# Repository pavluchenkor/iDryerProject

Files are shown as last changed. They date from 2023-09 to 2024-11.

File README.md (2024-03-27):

# Проект

Варианты сборки сушилки могут значительно отличаться. Сушилка iDryer может собираться как на одну так и на 10 катушек, в различных корпусах и разнообразными нагревательными элементами и вариантами обеспечения необходимой конвекции.

Ознакомьтесь с существующими решениями  

<div class="grid cards" markdown>
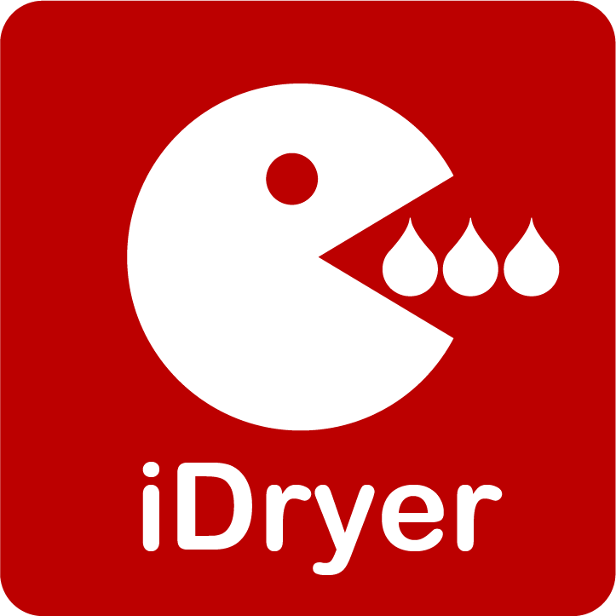
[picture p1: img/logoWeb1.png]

[Прошивка](/iDryerV2/Firmware/iDryerController/)  [:material-arrow-right-box:](/iDryerV2/Firmware/iDryerController/) 
</div>

<div class="grid cards" markdown>
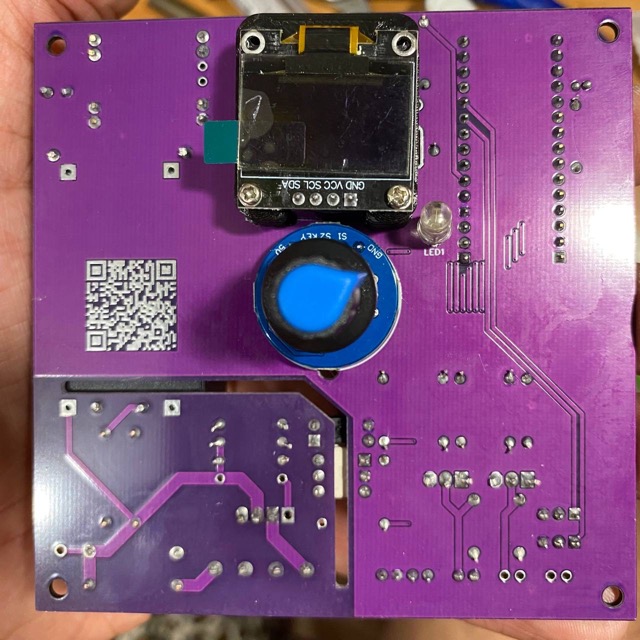
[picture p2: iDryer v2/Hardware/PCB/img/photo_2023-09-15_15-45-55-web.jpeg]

[Файлы печатной платы](/iDryerV2/Hardware/iDryerProject/iDryer%20v2/Hardware/PCB/)  [:material-arrow-right-box:](/iDryerV2/Hardware/iDryerProject/iDryer%20v2/Hardware/PCB/)           
</div>

<div class="grid cards" markdown>
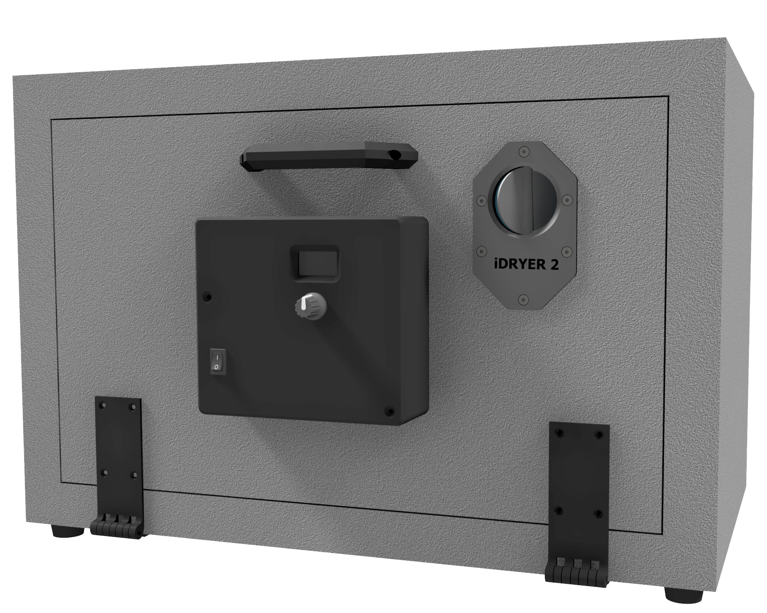
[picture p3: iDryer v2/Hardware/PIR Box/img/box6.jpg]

[Раскрой и инструкция по сборке корпуса из PIR плиты](/iDryerV2/Hardware/iDryerProject/iDryer%20v2/Hardware/PIR%20Box/)  [:material-arrow-right-box:](/iDryerV2/Hardware/iDryerProject/iDryer%20v2/Hardware/PIR%20Box/)                  
</div>

<div class="grid cards" markdown>
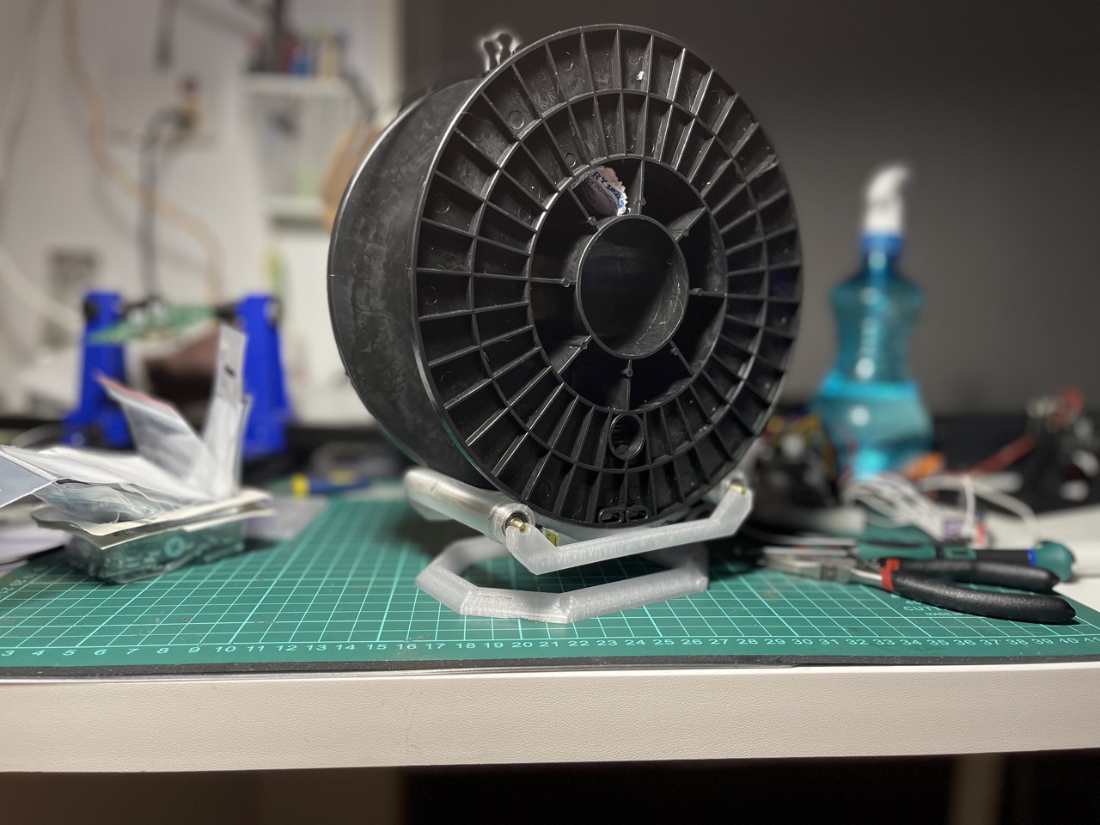
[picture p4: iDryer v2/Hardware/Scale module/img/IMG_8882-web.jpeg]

[Держатель катушек совмещенный с модулем весов](/iDryerV2/Hardware/iDryerProject/iDryer%20v2/Hardware/Scale%20module/)        [:material-arrow-right-box:](/iDryerV2/Hardware/iDryerProject/iDryer%20v2/Hardware/Scale%20module/)                           
</div>

<div class="grid cards" markdown>
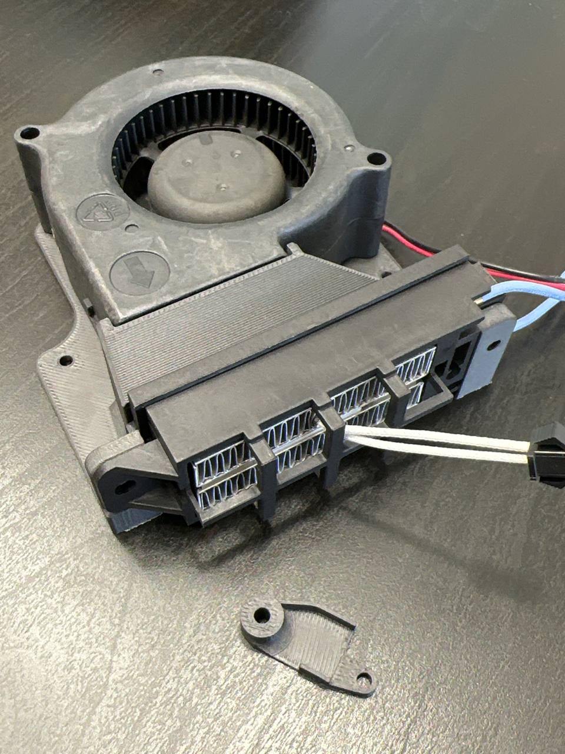
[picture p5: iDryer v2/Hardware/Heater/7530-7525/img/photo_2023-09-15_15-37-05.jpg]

[Сборка кулера 7530 и нагревательного элемента](/iDryerV2/Hardware/iDryerProject/iDryer%20v2/Hardware/Heater/7530-7525/)   [:material-arrow-right-box:](/iDryerV2/Hardware/iDryerProject/iDryer%20v2/Hardware/Heater/7530-7525/)                           
</div>

<div class="grid cards" markdown>
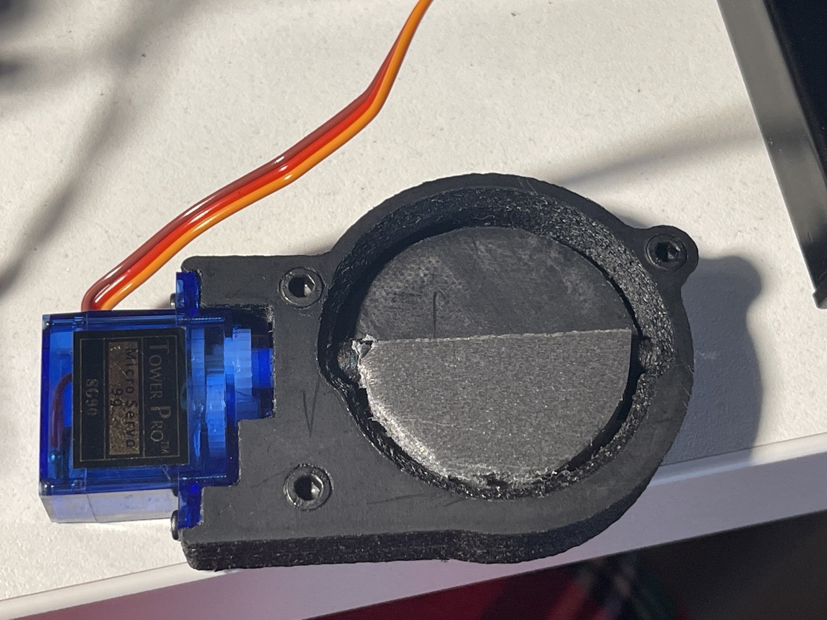
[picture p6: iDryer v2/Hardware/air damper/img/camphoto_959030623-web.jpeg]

[Воздушная заслонка v1](/iDryerV2/Hardware/iDryerProject/iDryer%20v2/Hardware/air%20damper/)  [:material-arrow-right-box:](/iDryerV2/Hardware/iDryerProject/iDryer%20v2/Hardware/air%20damper/)                                                             
</div>

<div class="grid cards" markdown>
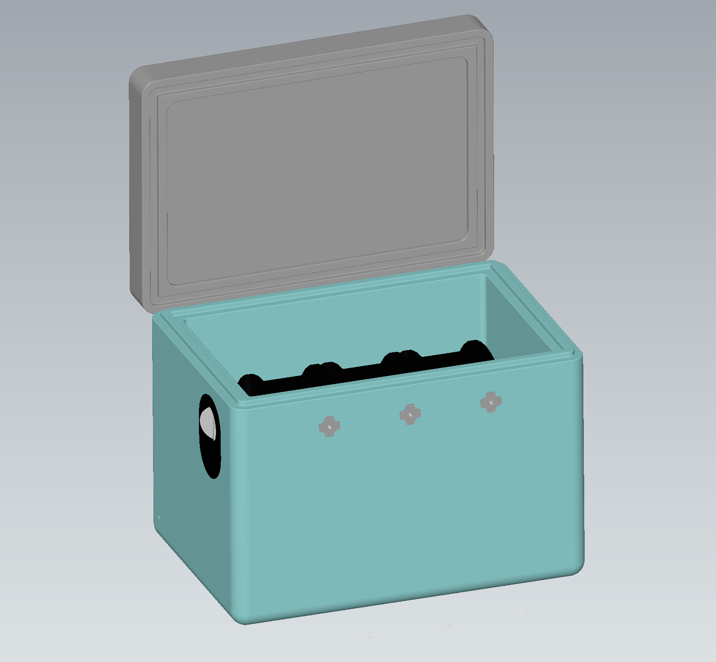
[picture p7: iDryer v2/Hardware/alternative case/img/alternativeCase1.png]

[Коробка из EPP, относительно ударопрочный и теплоизоляционный материал](/iDryerV2/Hardware/iDryerProject/iDryer%20v2/Hardware/alternative%20case/)      [:material-arrow-right-box:](/iDryerV2/Hardware/iDryerProject/iDryer%20v2/Hardware/alternative%20case/)                                                      
</div>

<div class="grid cards" markdown>
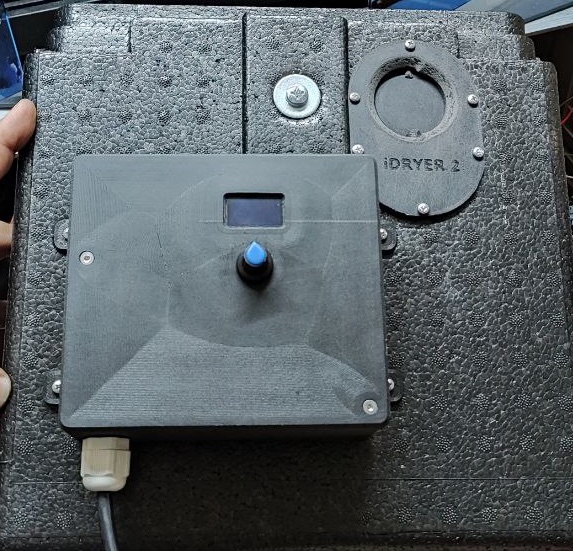
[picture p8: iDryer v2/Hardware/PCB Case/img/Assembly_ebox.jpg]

[Корпус контроллера, печатные детали](/iDryerV2/Hardware/iDryerProject/iDryer%20v2/Hardware/PCB%20Case/) [:material-arrow-right-box:](/iDryerV2/Hardware/iDryerProject/iDryer%20v2/Hardware/PCB%20Case/)                                                 
</div>

[группа в телеграмм :fontawesome-solid-paper-plane:](https://t.me/iDryer){ .md-button }

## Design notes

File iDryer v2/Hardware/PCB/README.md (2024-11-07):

**iDryer v2.1**

***Текущая версия***

Вы можете самостоятельно заказать изготовление печатной платы и приобрести необходимые компоненты. 
Если Вы имеете минимальный опыт пайки, то сборка не составит труда, все компоненты выводные и имеют крупный размер, а участники группы всегда помогут советом.

!!! warning annotate "Файлы для скачивания r2.1"

    PCB Design r2.1 [jlcpcb.com](https://oshwlab.com/svet_team/idryer_copy_copy)

    BOM для самостоятельной сборки r2.1 [google docs](https://docs.google.com/spreadsheets/d/1Y0MG9n_SadcK8cb_-e9J9ABQYqM_iH7iXZHlKbaz7wk/edit?usp=sharing)

## r2.1
<!-- ![печатная плата r2.1](https://raw.githubusercontent.com/pavluchenkor/iDryerProject/main/iDryer%20v2/Hardware/PCB/img/img2023-12-12-1.png){.image-container}<br>
![печатная плата r2.1](https://raw.githubusercontent.com/pavluchenkor/iDryerProject/main/iDryer%20v2/Hardware/PCB/img/img2023-12-12.png){.image-container}<br> <br> -->

<div class="image-container">
  <div class="custom-image">
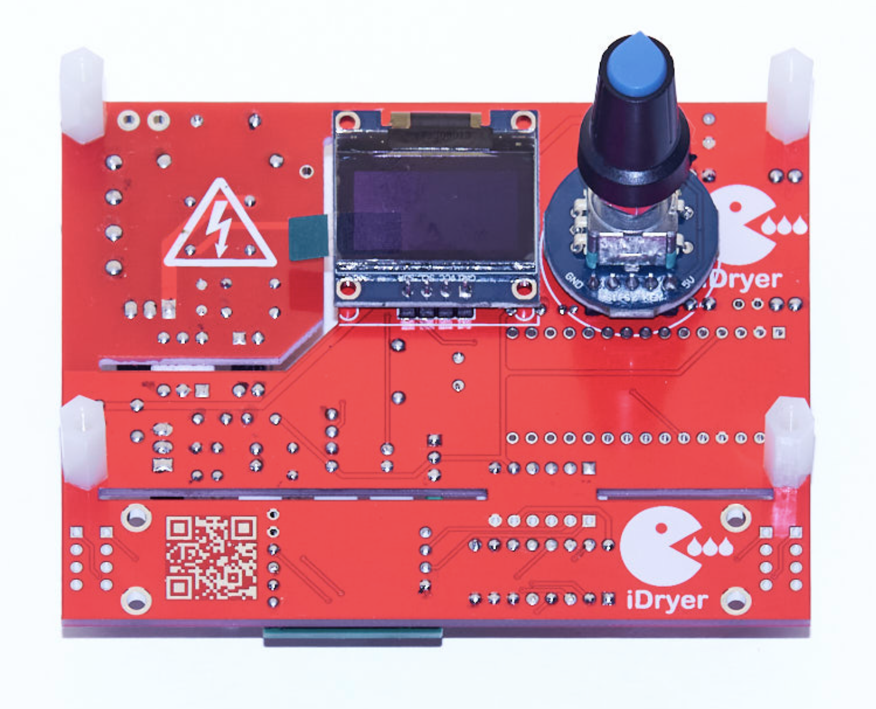
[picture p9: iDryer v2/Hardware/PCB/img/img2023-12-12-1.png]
    
  </div>
  <div class="custom-image">
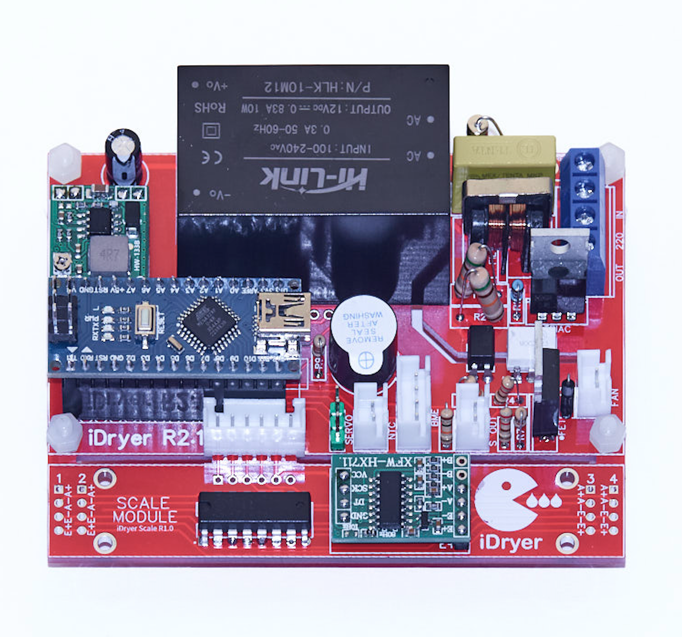
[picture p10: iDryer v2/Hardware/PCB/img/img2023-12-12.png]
    
  </div>
  <!-- <div class="custom-image">
    <img src="https://raw.githubusercontent.com/pavluchenkor/iDryerProject/main/iDryer%20v2/Hardware/PCB/img/img2023-12-12.png" alt="печатная плата r2.1">
  </div> -->
</div>

<div class="text-below-images">
Вы можете самостоятельно заказать изготовление печатной платы и приобрести необходимые компоненты. 
Если Вы имеете минимальный опыт пайки, то сборка не составит труда, все компоненты выводные и имеют крупный размер, а участники группы всегда помогут советом.

!!! warning annotate "Файлы для скачивания r2.1"
</div>

## r2

***Устаревшая версия без весов, датчика окончания филамента, но с поддержкой нагревателя 24В***

!!! warning annotate "Файлы для скачивания r2"

    PCB Design r2 [jlcpcb.com](https://oshwlab.com/svet_team/idryer)

    BOM для самостоятельной сборки r2 [google docs](https://docs.google.com/spreadsheets/d/13WdUZXiJUIk1PS-rFiE8_W3LRcMZVskWiTUnrRRYlAE/edit?usp=sharing)

<div class="image-container">
  <div class="custom-image">
    печатная плата r2
  </div>
  <div class="custom-image">
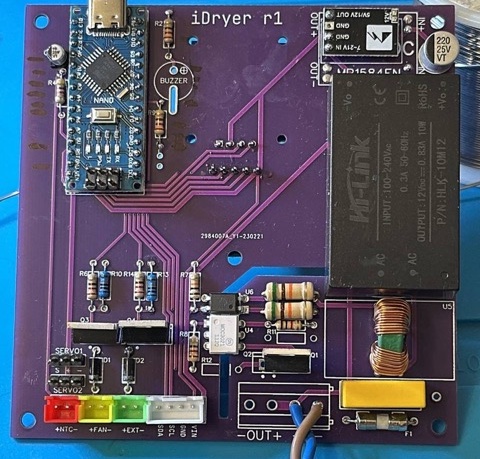
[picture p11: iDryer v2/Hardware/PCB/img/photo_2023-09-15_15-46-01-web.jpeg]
    
  </div>
</div>

<!-- ![печатная плата r2](https://raw.githubusercontent.com/pavluchenkor/iDryerProject/main/iDryer%20v2/Hardware/PCB/img/photo_2023-09-15_15-45-55-web.jpeg)<br>
![печатная плата r2](https://raw.githubusercontent.com/pavluchenkor/iDryerProject/main/iDryer%20v2/Hardware/PCB/img/photo_2023-09-15_15-46-01-web.jpeg)<br> -->

Фотографии можете посмотреть в нашей группе в телегам в этом посте:
[фото сборки участника группы](https://t.me/iDryer/3103)

[группа в телеграмм :fontawesome-solid-paper-plane:](https://t.me/iDryer){ .md-button }

[Contributing :material-file-edit:](https://github.com/pavluchenkor/iDryerProject/tree/main/iDryer%20v2/Hardware/PCB)

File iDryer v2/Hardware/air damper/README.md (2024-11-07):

# Заслонка


(*первородная заслонка*)

## Финальный вариант
Финальный вариант заслонки проветривания камеры. Данная модель рассчитана на толщину стенки сушилки 30мм. Но меняя толщину детали Диффузор можно подогнать под любой корпус. Монтаж упрощен - нужно вырезать сквозное шестигранное отверстие. Диффузор печатается с минимальным заполнением, что даёт хорошую теплоизоляцию.

!!! quote annotate "CAD файлы [от @gungrel](https://t.me/gungrel)"

    :material-download:</i> **[Заслонка Финал.stp](CAD/Заслонка Финал.stp)

## Старый вариант

предназначена для регулярного проветривания камеры

Потребуется покупка сервопривода [SG90 9g](https://aliexpress.ru/item/32962841728.html?sku_id=66666348213&spm=.search_results.16.6c0b4aa6tK2QUa)

!!! quote annotate "CAD файлы [от @gungrel](https://t.me/gungrel)"

    :material-download:</i> **[air damper.stp](CAD/air damper.stp)** - air damper.stp

<!-- ![img](https://raw.githubusercontent.com/pavluchenkor/iDryerProject/main/iDryer%20v2/Hardware/air%20damper/img/1.jpg){.img-left} -->

!!! quote annotate "Файлы для печати"

    :material-download:</i> **[air_damper_back.stl](CAD/air_damper_back.stl)** - air_damper_back.stl

    :material-download:</i> **[air_damper_diffuser.stl](CAD/air_damper_diffuser.stl)** - air_damper_diffuser.stl

    :material-download:</i> **[air_damper_flap.stl](CAD/air_damper_flap.stl)** - air_damper_flap.stl

    :material-download:</i> **[air_damper_front.stl](CAD/air_damper_front.stl)** - air_damper_front.stl
    
<!-- [разработано @gungrel](https://t.me/gungrel) -->

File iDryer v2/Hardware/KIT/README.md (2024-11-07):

# KIT



KIT набор iDryer v3 включает необходимые для самостоятельной сборки контроллера iDryer элементы, печатную плату, экран, энкодер и датчики, фрезерованные PIR панели для сборки в L-паз и шип-паз, металлические элементы пола и катушкодержателей. 
Все электронные компоненты выводные и крупные, удобны для сборки новичками и продвинутым любителями.

Как в собранном виде так и в виде набора для самостоятельной сборки.

[Состав коробки с электроникой](https://youtube.com/shorts/1hu8ouUc0jI?si=bNsCUIabV3f5F1-T)

[Сборка сушилки iDryer](https://www.youtube.com/watch?v=QL7AUkCoISA&list=PLv8eJa-BRh3z09ve9bOKYYc3aWBMgUUt0&index=1)
<br>
<br>
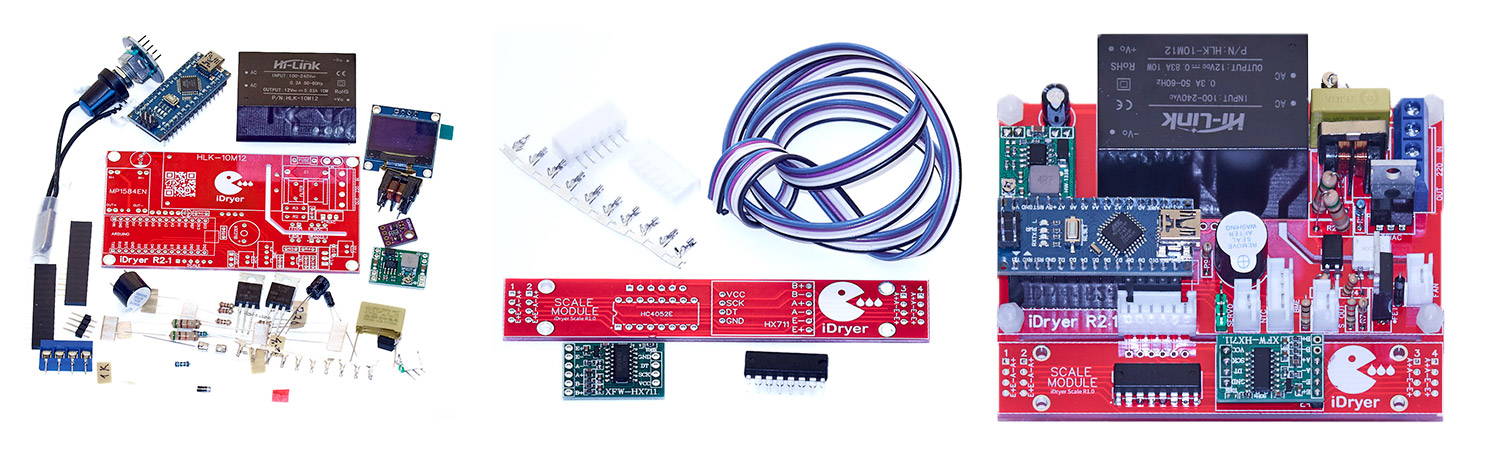
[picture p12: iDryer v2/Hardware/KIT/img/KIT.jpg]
KIT


!!! note annotate "Состав KIT полный"

    - Печатная плата
    - ARDUINO_NANO
    - OLED-128X64-I2C
    - Rotary Encoder EC11
    - Сервопривод SG-90 180 градусов
    - DC-DC Step Down MP1584 
    - HX711
    - BME-280
    - Thermostat NC 130C
    - BLS-4 2.54mm 30cm
    - BLS-5 2.54mm 30cm
    - XH-4P-2.54 30cm
    - Термистор
    - HLK-10M12
    - PTC керамический нагреватель (или) используется в сборке PIR
    - Кулер 7530
    - CD74HC4052E
    - MOC3023
    - 814
    - Active Buzzer 5V
    - Выключатель
    - 2А 250В
    - BT137-600E
    - N Channel FET IRF840
    - Filter 10MH
    - 0.1uF 280V
    - 220uF 16-25V
    - 10uF 5-16V
    - 1N4007
    - 51K 2W
    - 10K
    - 4,7K
    - 1K
    - 220
    - XH-4P-2.54
    - XH-2P-2.54
    - KF128L-5.08-4P
    - DB301V-3.5-2P
    - PLS-5 (encoder)
    - PLS-4 (oled) 
    - PLS-3 (servo) 
    - 100K 5% 3950
    - Rotary encoder ЕС11
    - GY-BME280-5В
    - Delta 7530 BFB0712H
    - Нагреватель 220V/100W
    - KSD9700 130C
    - XH2.54 4P
    - Dupont 4P 30cm разъем на проводе
    - Dupont 5P 30cm разъем на проводе
    - Серво SG90 180
    - KF128 5.08/4P
    - Панели корпуса
    - Пол  металлический 
    - Качеля катушкоджателя металлическая
    - Трубка алюминиевая 10х1 86мм
    - Подшипник 623 
    - Тензодатчик
    - Фиттинг
    - Кабель с вилкой

[Заказать :material-basket-plus:](https://store.idryer.org/){ .md-button }

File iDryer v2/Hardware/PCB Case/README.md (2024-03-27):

# Корпус контроллера r2

скачайте и распечатайте два файла [разработано @gungrel](https://t.me/gungrel)

<div class="image-container">
  <div class="custom-image">
    катушкодержатель
  </div>
  <div class="custom-image">
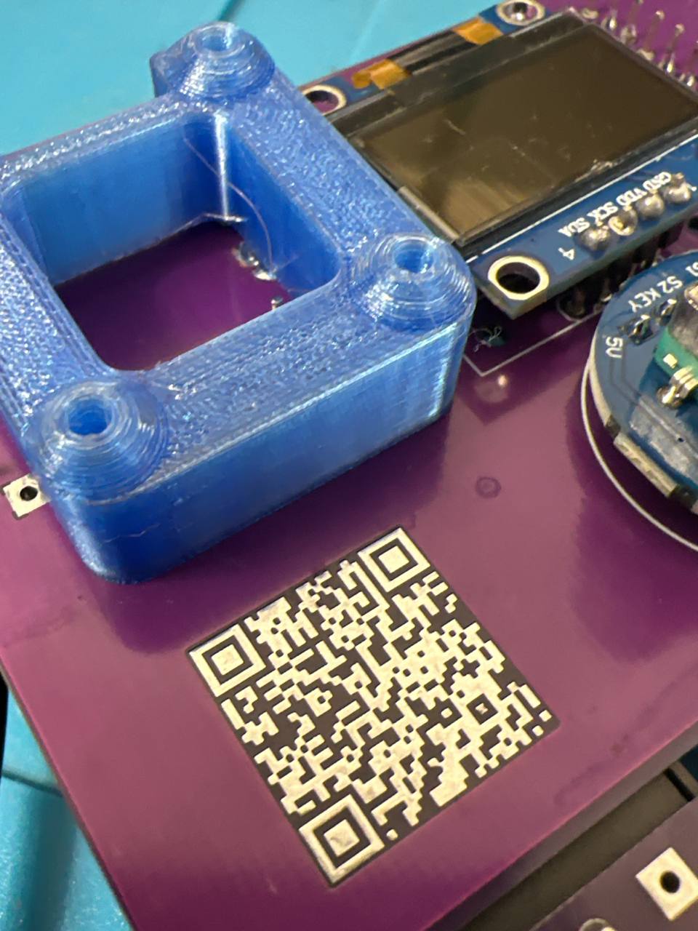
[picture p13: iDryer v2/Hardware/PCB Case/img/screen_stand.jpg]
    
  </div>
</div>

<!-- ![Разметка](https://raw.githubusercontent.com/pavluchenkor/iDryerProject/main/iDryer%20v2/Hardware/PCB%20Case/img/Assembly_ebox.jpg){.img-left-50}
![Разметка](https://raw.githubusercontent.com/pavluchenkor/iDryerProject/main/iDryer%20v2/Hardware/PCB%20Case/img/screen_stand.jpg){.img-left-50} -->

## Файлы

!!! quote annotate "Файлы для печати"

    :material-download:</i> **[iDryer v1 prototype](CAD/Assembly_ebox.stp)** - Корпус
    
    :material-link:</i>** [iDryer v2](CAD/screen_stand.stp)** - пороставка экрана

[Contributing :material-file-edit:](https://github.com/pavluchenkor/iDryerProject/blob/main/iDryer%20v2/Hardware/alternative%20case/)

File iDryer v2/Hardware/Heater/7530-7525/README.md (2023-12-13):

# Нагреватель  с кулером
Разметка<br>

Модуль от [@gungrel](https://t.me/gungrel)

!!! quote annotate "Файлы для печати"

    :material-download:</i> **[Крепление бме280.stl](CAD/Крепление бме280.stl)** - Крепление бме280.stl
    
    :material-link:</i>** [Модуль нагревателя PTC 100W 220V 7530 7525.stp](CAD/Модуль нагревателя PTC 100W 220V 7530 7525.stp)** - Модуль нагревателя

## Покупка комплектующих

<!-- [Вентилятор для модуля на али](https://aliexpress.ru/item/1691802504.html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)

[2 вентилятора для модуля на али](https://aliexpress.ru/item/1005002255060284.html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)

[Нагревательный элемент на али](https://aliexpress.ru/item/32319632955.html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) -->

[Contributing :material-file-edit:](https://github.com/pavluchenkor/iDryerProject/tree/main/iDryer%20v2/Hardware/Heater/7530-7525)

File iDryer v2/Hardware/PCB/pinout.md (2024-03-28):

# Pinout

<div class="image-container">
  <div class="custom-image">
    iDryer сборка контроллера сушилки филамента
  </div>
</div>

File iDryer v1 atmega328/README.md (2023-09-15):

**iDryer v1**

<a href="https://t.me/iDryer">
  Telegram
</a>

**[группа в телеграмм](https://t.me/iDryer)**

[группа в телеграмм](https://t.me/iDryer)

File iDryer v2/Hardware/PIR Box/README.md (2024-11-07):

# Корпус из PIR

PIR плита является дешевым и доступным материалом для изготовления корпуса сушилки. 
## Плюсы
- цена
- удобство и простота обработки
- приемлемый внешний вид
- теплопроводность одна из самых низких среди теплоизоляционных материалов
- отсутствие выделяемых вредных веществ при нагревании

## Минусы
- можно деформировать при ударе 

<div class="image-container">
  <div class="custom-image">
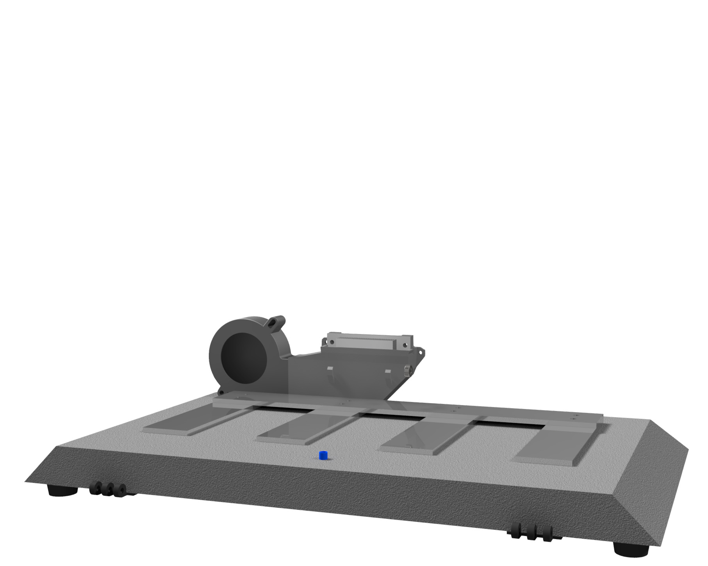
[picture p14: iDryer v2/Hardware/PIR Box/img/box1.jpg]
iDryer сборка корпуса
    
  </div>
  <div class="custom-image">
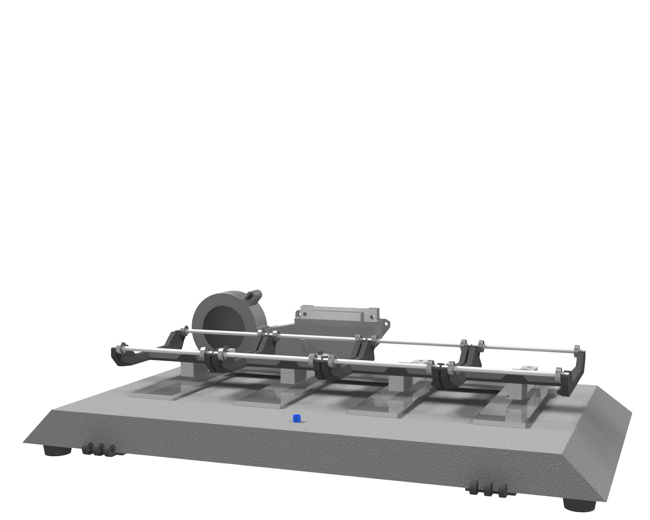
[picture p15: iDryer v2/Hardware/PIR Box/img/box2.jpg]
iDryer сборка корпуса
    
  </div>
</div>

<div class="image-container">
  <div class="custom-image">
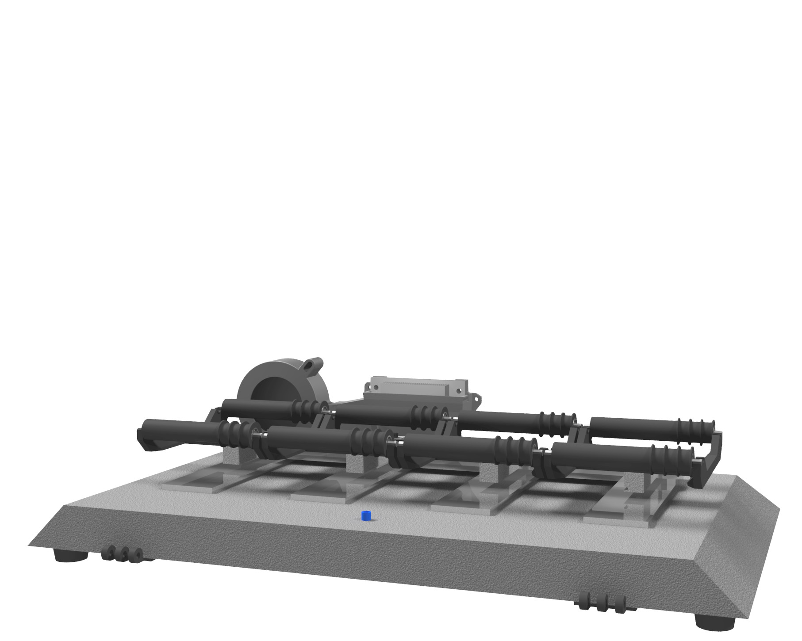
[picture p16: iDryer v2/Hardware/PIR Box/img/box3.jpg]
iDryer сборка корпуса
    
  </div>
  <div class="custom-image">
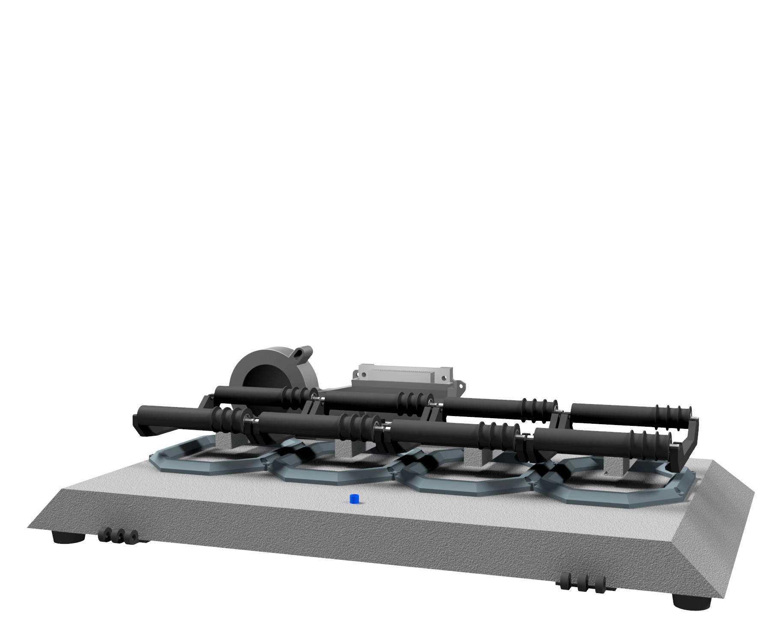
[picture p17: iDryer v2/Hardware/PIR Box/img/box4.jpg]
iDryer сборка корпуса
    
  </div>
</div>

<div class="image-container">
  <div class="custom-image">
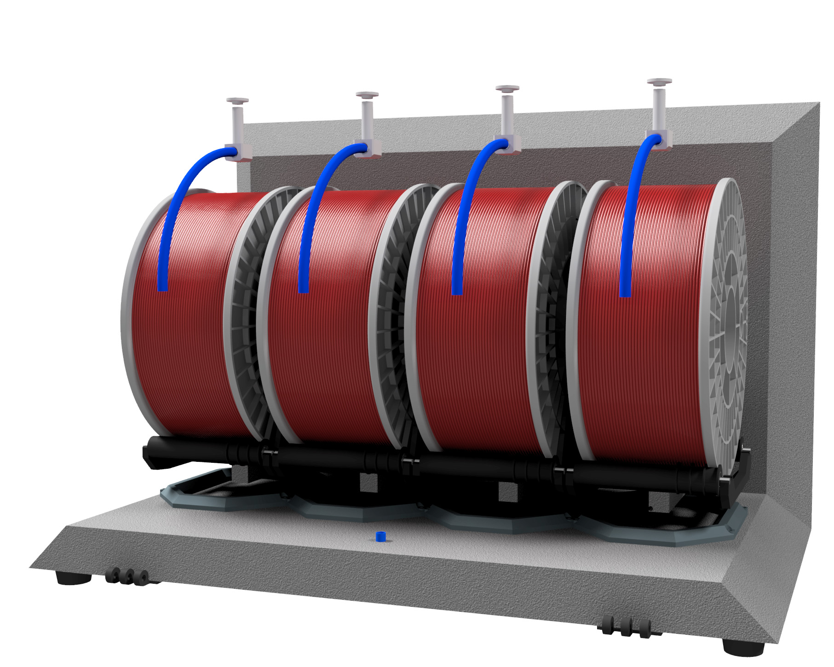
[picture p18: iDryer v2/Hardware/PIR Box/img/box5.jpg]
iDryer сборка корпуса
    
  </div>
  <div class="custom-image">
    iDryer сборка корпуса
  </div>
</div>
<!-- 

<!-- ![Разметка](https://raw.githubusercontent.com/pavluchenkor/iDryerProject/main/iDryer%20v2/Hardware/PIR%20Box/img/box1.jpg)
![Разметка](https://raw.githubusercontent.com/pavluchenkor/iDryerProject/main/iDryer%20v2/Hardware/PIR%20Box/img/box2.jpg)
![Разметка](https://raw.githubusercontent.com/pavluchenkor/iDryerProject/main/iDryer%20v2/Hardware/PIR%20Box/img/box3.jpg)
![Разметка](https://raw.githubusercontent.com/pavluchenkor/iDryerProject/main/iDryer%20v2/Hardware/PIR%20Box/img/box4.jpg)
![Разметка](https://raw.githubusercontent.com/pavluchenkor/iDryerProject/main/iDryer%20v2/Hardware/PIR%20Box/img/box5.jpg)
![Разметка](https://raw.githubusercontent.com/pavluchenkor/iDryerProject/main/iDryer%20v2/Hardware/PIR%20Box/img/box6.jpg) -->
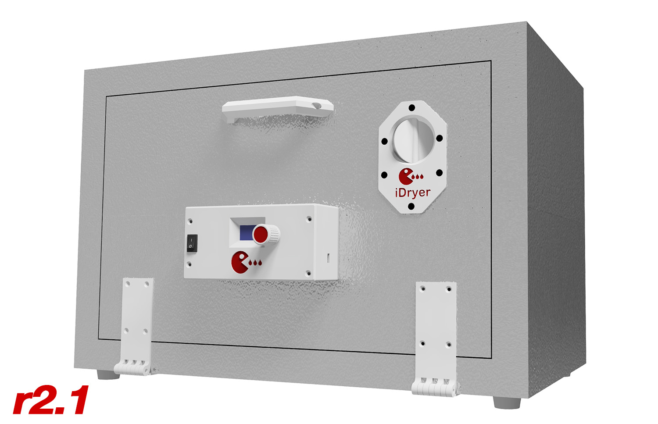
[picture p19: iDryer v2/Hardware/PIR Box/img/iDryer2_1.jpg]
iDryer


!!! quote annotate "Полная модель корпуса"

    :material-download:</i> **[PIR_box_assembly_r2_1.stp](CAD/PIR_box_assembly_r2_1.stp)** - наиболее дешевым из оптимальных материалов является ABS CF10, он прост в печати, не требует камеры
    и прекрасно справляется с рабочей температурой сушилки. Именно из ABS CF10 распечатаны и катушкодержатели и даже воздуховод к которому прикреплен радиатор обогрева.

!!! warning annotate "Важно"

    Все детали находящиеся внутри корпуса печатаются из материалов выдерживающих нагревание 100С и выше.

## Изготовление (время ~60 минут)
- ознакомьтесь изображениями
- распечатайте файл "Раскрой.pdf"
- распечатайте "Оснастка ножа.stp" 
- разметьте лист
- нарежьте детали
- срежьте фаски где это необходимо
- склейте (для склеивания подходит специальный клей-пена для PIR плит или любой клей на полиуретановой  основе)
- проклейте торцы и стыки алюминиевым скотчем
- распечатайте петли, приклейте на тонкий двусторонний скотч к корпусу и двери, скрутите саморезами(размер самореза 25-30мм в длину и 4-5 в диаметре) такое соединение работает у меня без нареканий

!!! quote annotate "Файлы для скачивания"

    :material-download:</i> **[Оснастка ножа.stp](CAD/Оснастка ножа.stp)** - Оснастка ножа
    
    :material-download:</i>** [Раскрой.pdf](CAD/Раскрой.pdf)** - Раскрой

!!! warning annotate "Важно"

    Обратите внимание! Задняя стенка склеивается из двух частей в целях оптимизации раскроя

<div class="image-container">
  <div class="custom-image">
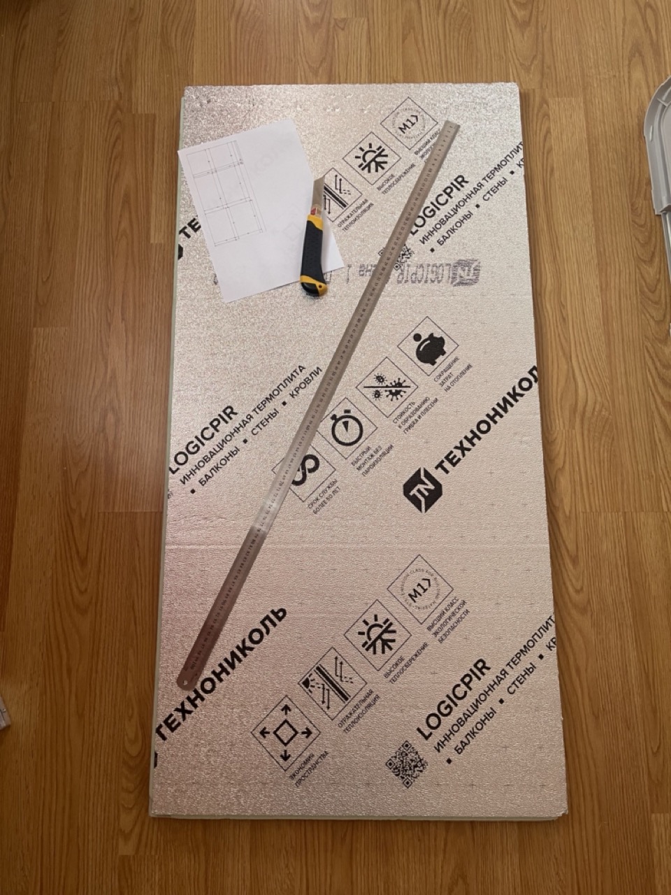
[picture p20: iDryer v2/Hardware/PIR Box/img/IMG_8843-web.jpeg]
iDryer сборка корпуса
    
  </div>
  <div class="custom-image">
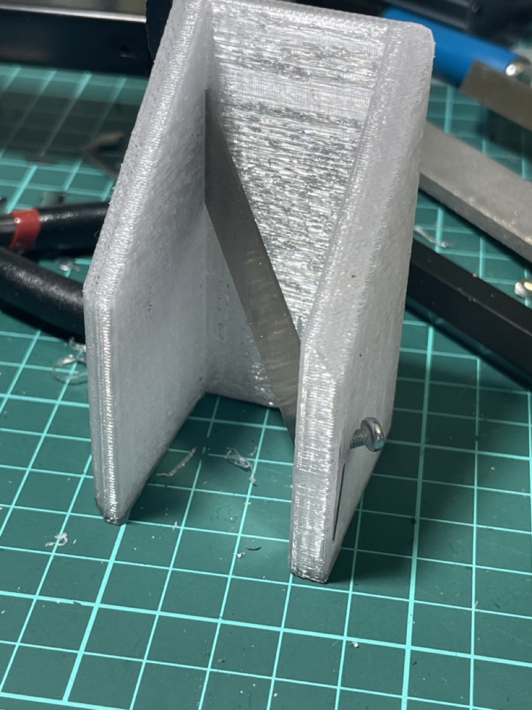
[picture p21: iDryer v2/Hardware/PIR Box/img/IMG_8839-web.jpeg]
iDryer сборка корпуса
    
  </div>
</div>

<div class="image-container">
  <div class="custom-image">
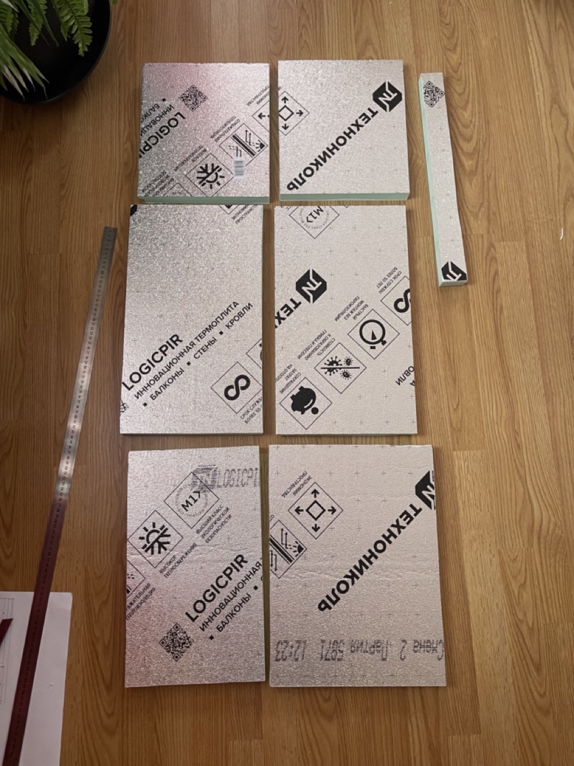
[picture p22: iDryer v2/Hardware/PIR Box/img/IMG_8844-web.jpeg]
iDryer сборка корпуса
    
  </div>
  <div class="custom-image">
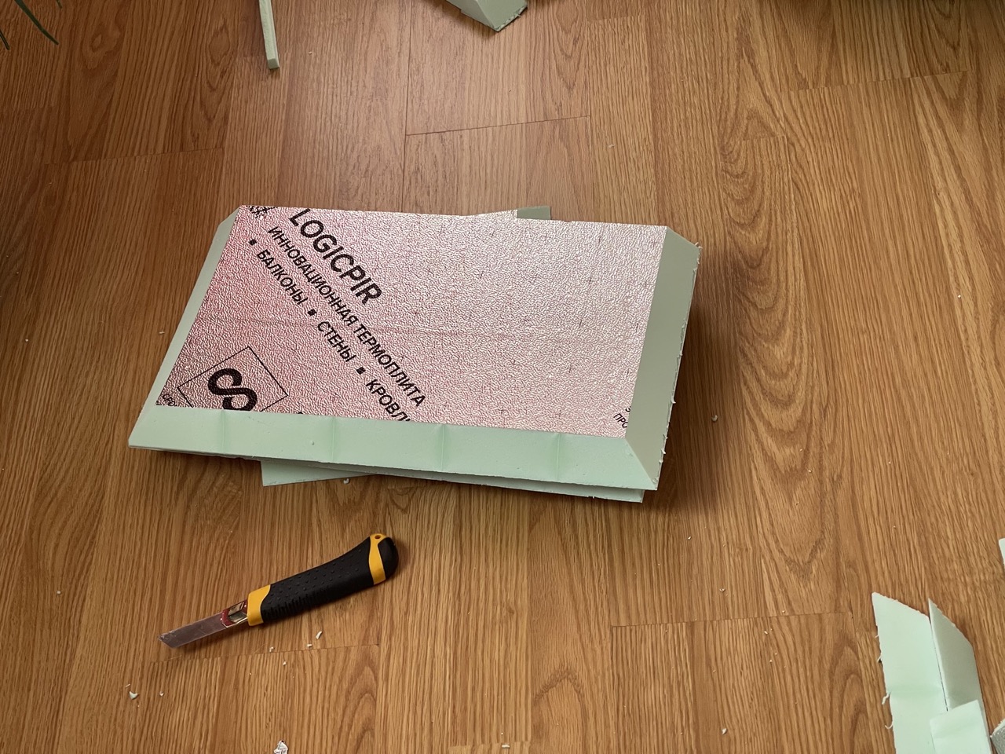
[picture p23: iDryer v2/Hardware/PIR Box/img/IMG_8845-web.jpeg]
iDryer сборка корпуса
    
  </div>
</div>

<div class="image-container">
  <div class="custom-image">
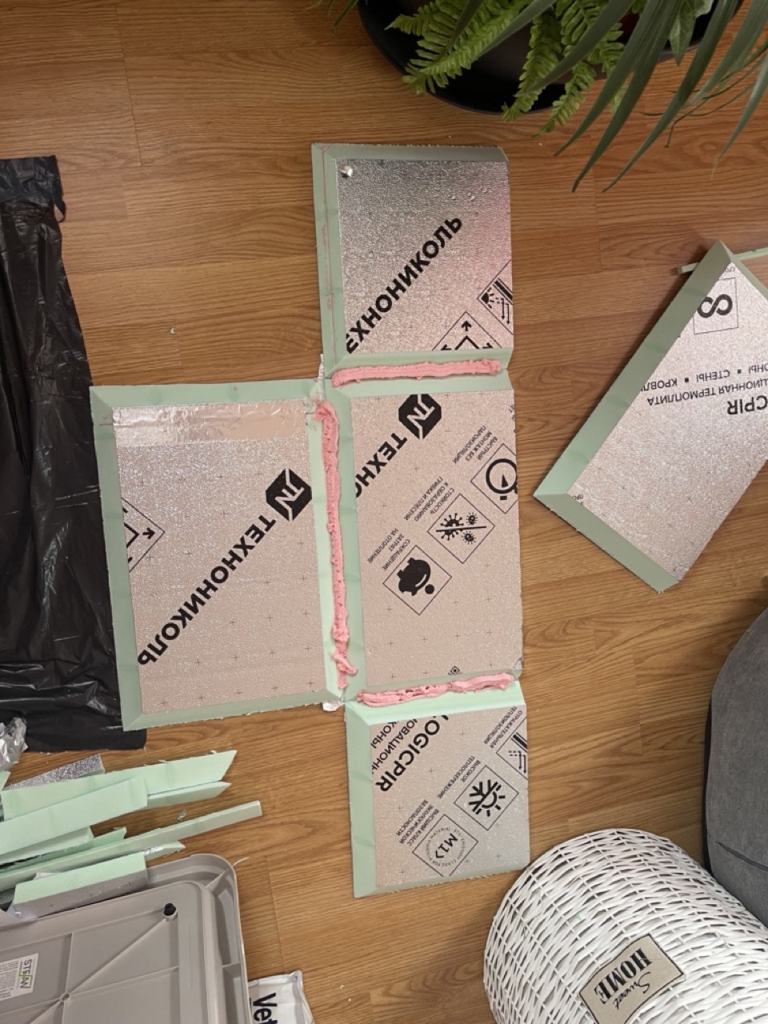
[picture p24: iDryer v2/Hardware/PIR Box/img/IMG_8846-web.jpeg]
iDryer сборка корпуса
    
  </div>
  <div class="custom-image">
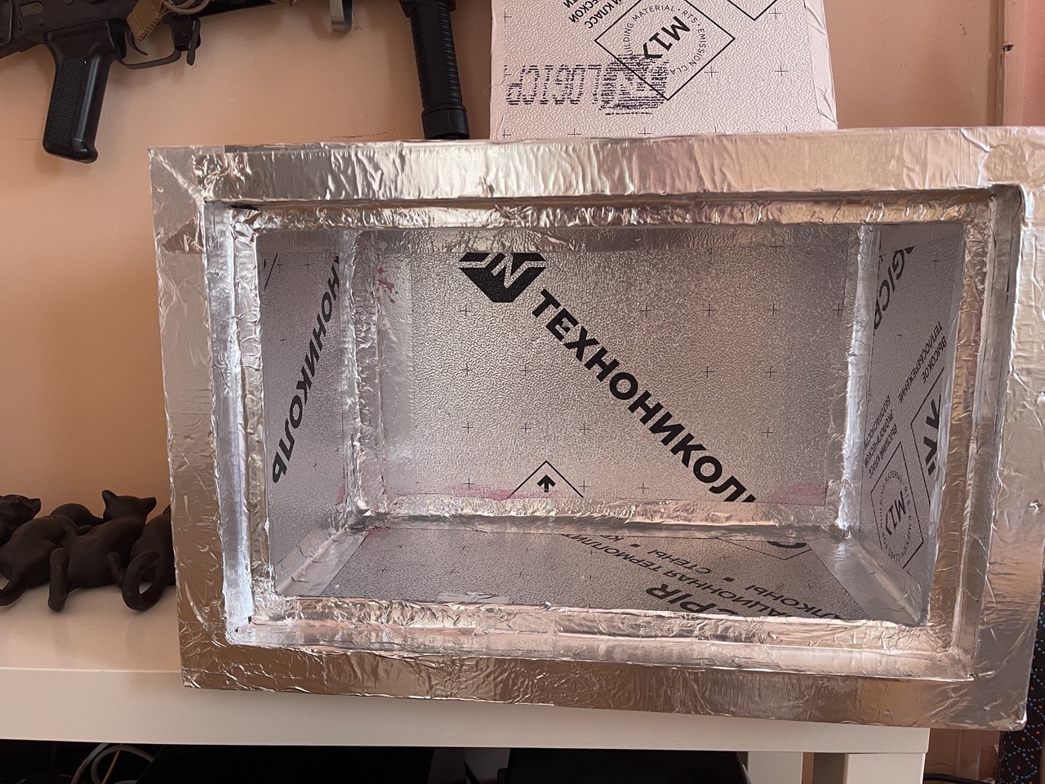
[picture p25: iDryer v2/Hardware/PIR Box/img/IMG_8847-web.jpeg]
iDryer сборка корпуса
    
  </div>
</div>

<div class="image-container">
  <div class="custom-image">
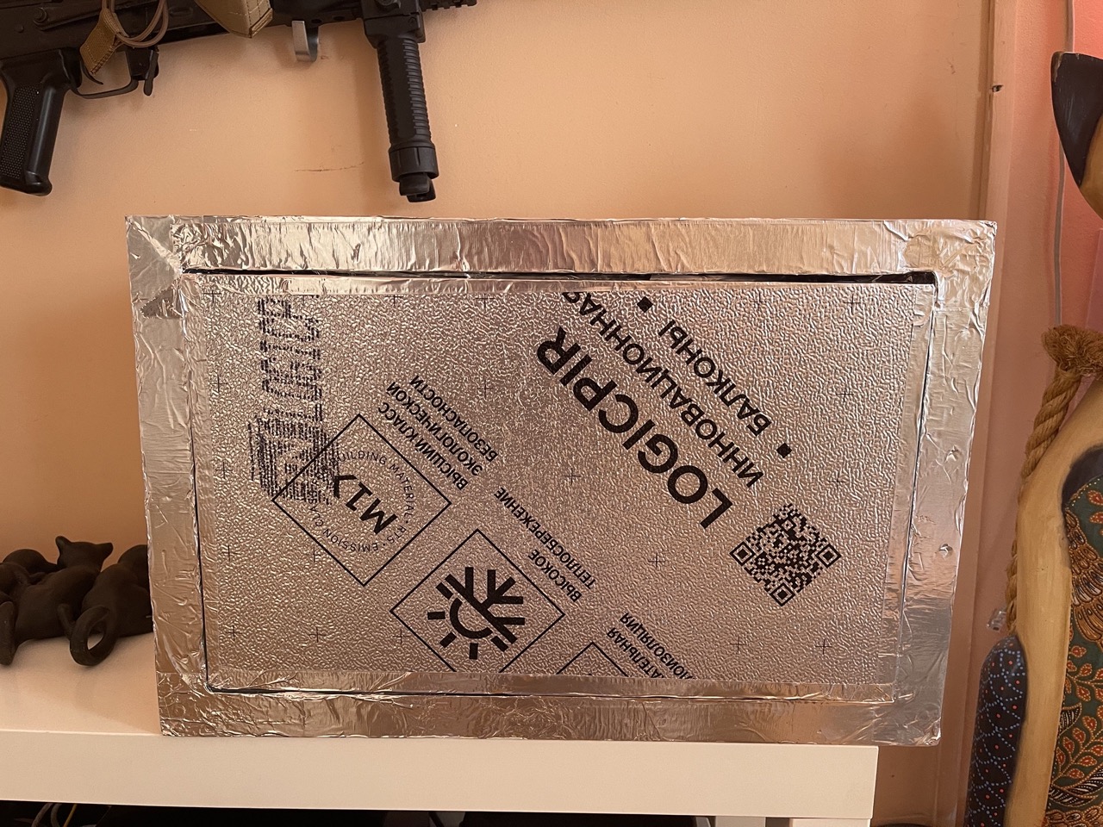
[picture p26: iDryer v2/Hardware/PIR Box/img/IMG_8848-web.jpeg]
iDryer сборка корпуса
    
  </div>
  <div class="custom-image">
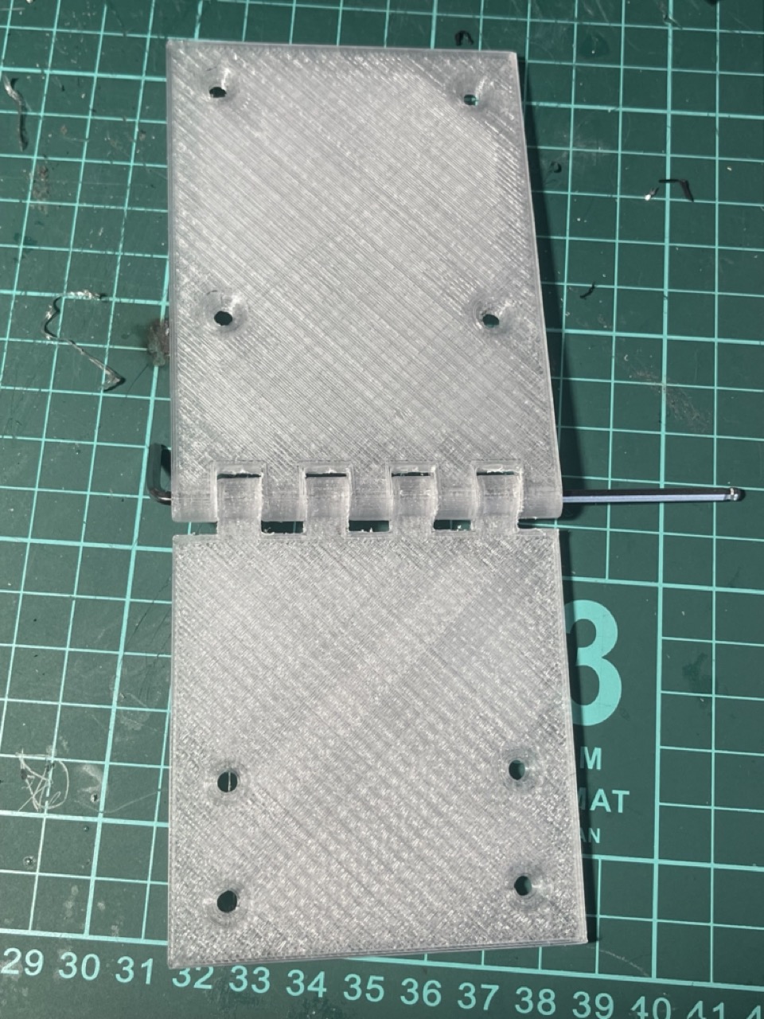
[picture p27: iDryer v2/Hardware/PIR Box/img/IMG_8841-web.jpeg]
iDryer сборка корпуса
    
  </div>
</div>

<div class="image-container">
  <div class="custom-image">
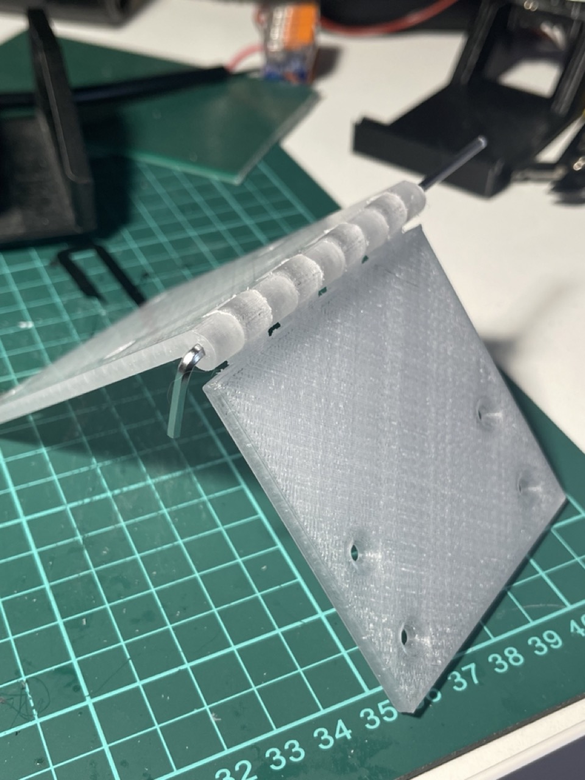
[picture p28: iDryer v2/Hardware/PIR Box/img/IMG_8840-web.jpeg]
iDryer сборка корпуса
    
  </div>
  <div class="custom-image">
    iDryer сборка корпуса
  </div>
</div>

<!-- ![Разметка](https://raw.githubusercontent.com/pavluchenkor/iDryerProject/main/iDryer%20v2/Hardware/PIR%20Box/img/IMG_8843-web.jpeg){.img-padding}

![Нож для резки](https://raw.githubusercontent.com/pavluchenkor/iDryerProject/main/iDryer%20v2/Hardware/PIR%20Box/img/IMG_8839-web.jpeg){.img-padding}

![Нарезка](https://raw.githubusercontent.com/pavluchenkor/iDryerProject/main/iDryer%20v2/Hardware/PIR%20Box/img/IMG_8844-web.jpeg){.img-padding}

![Подрезка углов](https://raw.githubusercontent.com/pavluchenkor/iDryerProject/main/iDryer%20v2/Hardware/PIR%20Box/img/IMG_8845-web.jpeg){.img-padding}

![Склеивание](https://raw.githubusercontent.com/pavluchenkor/iDryerProject/main/iDryer%20v2/Hardware/PIR%20Box/img/IMG_8846-web.jpeg){.img-padding}

![Готовый корпус](https://raw.githubusercontent.com/pavluchenkor/iDryerProject/main/iDryer%20v2/Hardware/PIR%20Box/img/IMG_8847-web.jpeg){.img-padding} -->

<!-- ![Готовый корпус](https://raw.githubusercontent.com/pavluchenkor/iDryerProject/main/iDryer%20v2/Hardware/PIR%20Box/img/IMG_8848-web.jpeg){.img-padding}

![Петля](https://raw.githubusercontent.com/pavluchenkor/iDryerProject/main/iDryer%20v2/Hardware/PIR%20Box/img/IMG_8841-web.jpeg){.img-padding}

![Петля](https://raw.githubusercontent.com/pavluchenkor/iDryerProject/main/iDryer%20v2/Hardware/PIR%20Box/img/IMG_8840-web.jpeg){.img-padding} -->

[Contributing :material-file-edit:](https://github.com/pavluchenkor/iDryerProject/tree/main/iDryer%20v2/Hardware/PIR%20Box)

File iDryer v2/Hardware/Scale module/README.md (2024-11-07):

# Катушкодержатель



Предназначен для хранения катушек и отслеживания остатка филамента, отображения остатка на экране и сигнализации через сигнальный выход

## Печатный вариант
Верхняя часть модуля является удобной альтернативой существующим держателям катушек.
Используются 694 подшипники или их аналоги (11х4х4) и бронзовый прут d4 из хозяйственного магазина в качестве оси.
Печатается из композитного ABS или любого пластика способного выдерживать максимальную планируемую температуру сушки + 10-15 градусов.

Потребуется покупка [load cell module и HX711](https://aliexpress.ru/item/32860114708.html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)

Модели легко переделать под имеющиеся в наличии подшипники

!!! quote annotate "Файлы для печати на 3д принтере"

    :material-download:</i> **[Весы узкие.stp](CAD/for%203D%20printing/Весы узкие.stp)**
    
    :material-download:</i>** [Весы.stp](CAD/for%203D%20printing/Весы.stp)**

<div class="image-container">
  <div class="custom-image">
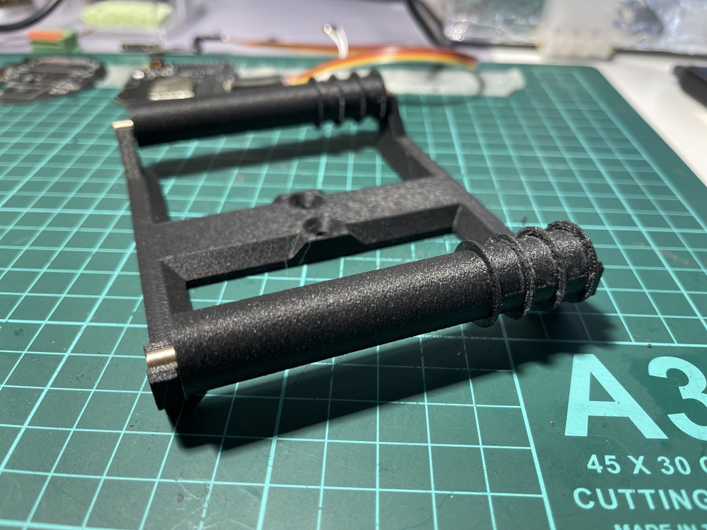
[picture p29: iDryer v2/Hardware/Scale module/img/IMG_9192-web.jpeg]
    
  </div>
  <div class="custom-image">
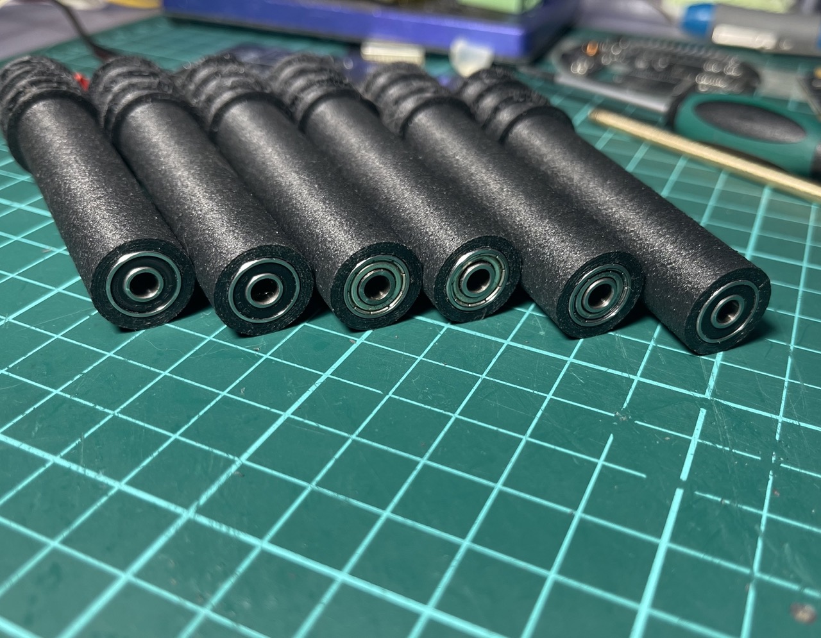
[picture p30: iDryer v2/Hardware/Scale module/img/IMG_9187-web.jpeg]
    
  </div>
  <div class="custom-image">
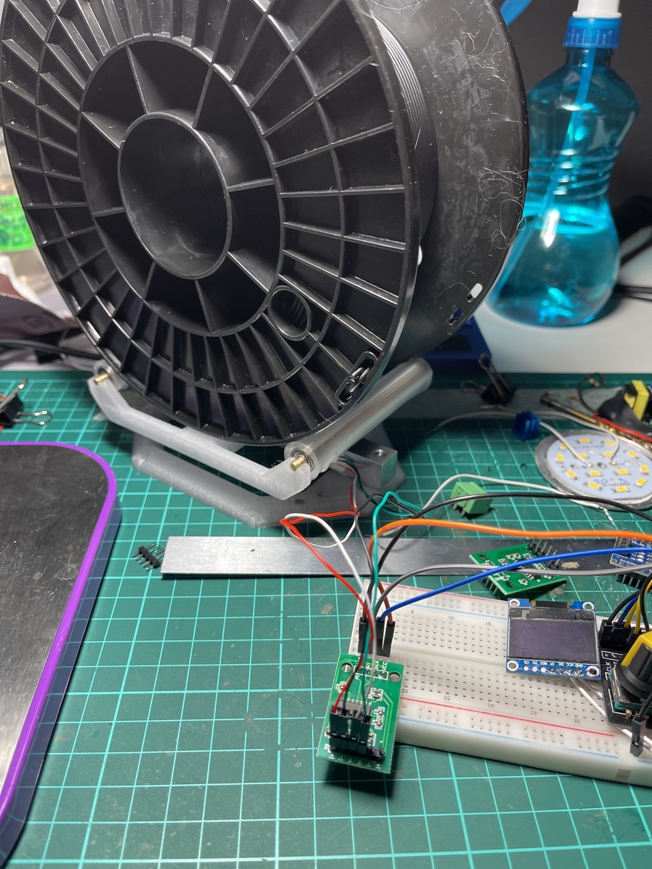
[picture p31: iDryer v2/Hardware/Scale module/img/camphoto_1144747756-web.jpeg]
    
  </div>
</div>

<div class="image-container">
  <div class="custom-image">
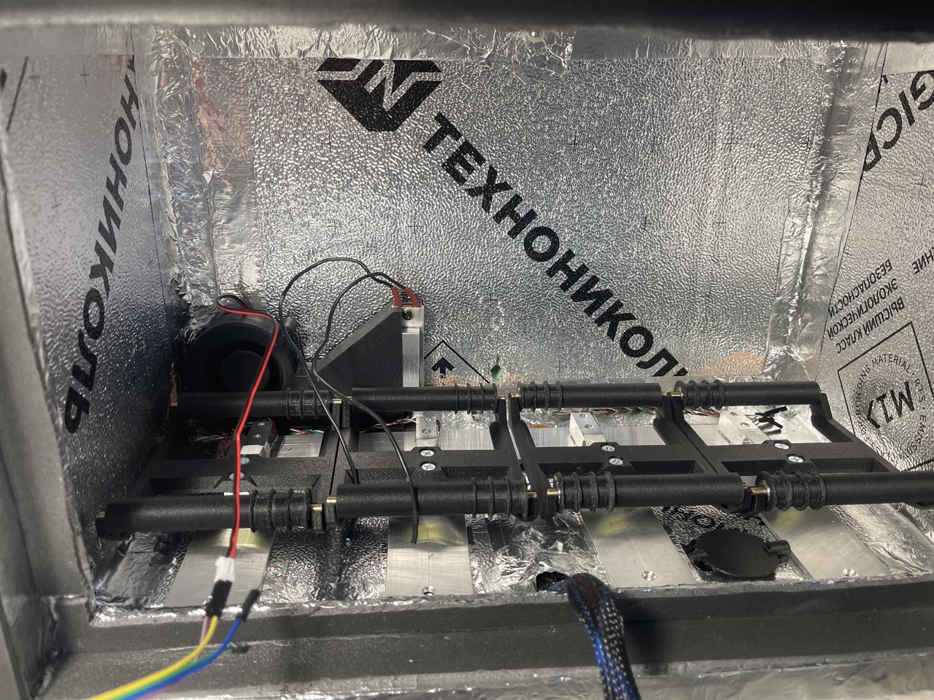
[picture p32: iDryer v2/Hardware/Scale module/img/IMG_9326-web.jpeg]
    
  </div>
  <div class="custom-image">
    катушкодержатель
  </div>
</div>

<!-- ![img](https://raw.githubusercontent.com/pavluchenkor/iDryerProject/main/iDryer%20v2/Hardware/Scale%20module/img/IMG_9192-web.jpeg)<br>
![img](https://raw.githubusercontent.com/pavluchenkor/iDryerProject/main/iDryer%20v2/Hardware/Scale%20module/img/IMG_9187-web.jpeg)<br>
![img](https://raw.githubusercontent.com/pavluchenkor/iDryerProject/main/iDryer%20v2/Hardware/Scale%20module/img/camphoto_1144747756-web.jpeg)<br>
<!-- ![img](https://raw.githubusercontent.com/pavluchenkor/iDryerProject/main/iDryer%20v2/Hardware/Scale%20module/img/camphoto_959030623-web.jpeg)<br>
![img](https://raw.githubusercontent.com/pavluchenkor/iDryerProject/main/iDryer%20v2/Hardware/Scale%20module/img/camphoto_1483920592-web.jpeg)<br> -->
<!-- ![img](https://raw.githubusercontent.com/pavluchenkor/iDryerProject/main/iDryer%20v2/Hardware/Scale%20module/img/IMG_9326-web.jpeg)<br>
![img](https://raw.githubusercontent.com/pavluchenkor/iDryerProject/main/iDryer%20v2/Hardware/Scale%20module/img/IMG_9209-web.jpeg)<br> -->

## Металлические варианты
 Участниками группы разработано несколько вариантов из металла. 

### От @gungrel
Катушкодержатель металл гибка под подшипники 623. В сборке основания под 1,2,3 и 4 катушки. В качестве ролика используется трубка алюминиевая 12х1

!!! quote annotate "Модель для лазерной резки и гибки [от @gungrel](https://t.me/gungrel)"
    
    :material-download:</i>** [Катушкодержатель гибка финал.stp](CAD/for%20cutting%20metal/Катушкодержатель гибка финал.stp)
<br>
### Ремикс [от @Kekht](https://t.me/Kekht)
*на раннюю версию держателя [от @gungrel](https://t.me/gungrel)*

**Особенности модификации:**

  Максимальная ширина катушки - 83.6мм

  Используются подшипники 686 и алюминиевая трубка - диаметр внешний 15мм внутренний 13мм

  Для крепления подшипников используются печатные анкерные вставки и винты М3
  
  Диаметр отверстия под анкера 8мм, поэтому изменив только акнеры возможно использования любых подшипников и трубок (максимальный диаметр трубки 23мм)
  
  Анкера лучше печатать из полиамида (чистого или композитного). При необходимости снять ролики после выкручивания винтов анкера извлекаются без усилий
  
  По бокам держателя есть дополнительные отверстия, к которым можно крепить стойки-держатели для нестандартных катушек (картонных например) или пробников
  
  Предусмотрена проставка под тензодатчик, позволяющая дополнительно закрепить на стяжку его провода
  
  Предусмотрены отверстия для крепления ножек (в модели два варианта) или специальных крепежных печатных пластин (тоже два варианта под разный тип винтов), позволяющих скреплять держатели в "батарею".

    Раскрой сделан под гибку со следующими параметрами:
    Радиус для 3мм стали -  2,7
    Радиус для 2мм стали - 1,8
    Минимальная полка - 14мм
    Коэф.К - 0,44
  
<div class="video-wrapper">
  <iframe width="1280" height="720" src="https://www.youtube.com/embed/iAZZLo_1NXo?si=j_zRWY-Wy7RiXFXJ" frameborder="0" allowfullscreen></iframe>
</div>

!!! quote annotate "Ремикс [от @Kekht](https://t.me/Kekht) на раннюю версию держателя [от @gungrel](https://t.me/gungrel)"
    
    :material-download:</i>** [SpoolHolderWeightModule_v1_3_2.STEP](CAD/for%20cutting%20metal/[SpoolHolderWeightModule_v1_3_2.STEP])

    :material-download:</i>** [Rollers_Holder_v1_3.DXF](CAD/for%20cutting%20metal/[Rollers_Holder_v1_3.DXF])
    
    :material-download:</i>** [Base_Single_v1_2.DXF](CAD/for%20cutting%20metal/[Base_Single_v1_2.DXF])

### Вариант от Саши

<!-- ![img](https://raw.githubusercontent.com/pavluchenkor/iDryerProject/main/iDryer%20v2/Hardware/Scale%20module/img/Sasha1.jpg){.img-left-50}
![img](https://raw.githubusercontent.com/pavluchenkor/iDryerProject/main/iDryer%20v2/Hardware/Scale%20module/img/Sasha2.jpg){.img-left-50}<br><br> -->

<div class="image-container">
  <div class="custom-image">
    катушкодержатель
  </div>
  <div class="custom-image">
    катушкодержатель
  </div>
  <!-- <div class="custom-image">
    <img src="https://raw.githubusercontent.com/pavluchenkor/iDryerProject/main/iDryer%20v2/Hardware/PCB/img/img2023-12-12.png" alt="печатная плата r2.1">
  </div> -->
</div>

!!! quote annotate "Модель для фрезеровки"

    :material-download:</i> **[Sasha.STEP](CAD/for%20cutting%20metal/Sasha.STEP)
      
    [разработано Саша](https://t.me/iDryer/9446)

[Contributing :material-file-edit:](https://github.com/pavluchenkor/iDryerProject/tree/main/iDryer%20v2/Hardware/Scale%20module)

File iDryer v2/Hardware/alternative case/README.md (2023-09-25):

# Корпус из EPP

Корпус сушилки из EPP (экструзионный полипропилен)

Полипропилен имеет низкое влагопоглощение. Характеризуется хорошими электроизоляционными свойствами в широком диапазоне температур.
Максимальная температура эксплуатации 120 °C
На рынке представлен широкий ассортимент готовых коробов разных размеров.



Обсуждение тут

[Группа:fontawesome-solid-paper-plane:](https://t.me/iDryer){ .md-button }

[Обсуждение 2 :fontawesome-solid-paper-plane:](https://t.me/iDryer/2175)

[Обсуждение 3 :fontawesome-solid-paper-plane:](https://t.me/iDryer/2304)

[Обсуждение 4 :fontawesome-solid-paper-plane:](https://t.me/iDryer/1244)

[Обсуждение 5 :fontawesome-solid-paper-plane:](https://t.me/iDryer/1244)

[Contributing :material-file-edit:](https://github.com/pavluchenkor/iDryerProject/tree/main/iDryer%20v2/Hardware/alternative%20case)

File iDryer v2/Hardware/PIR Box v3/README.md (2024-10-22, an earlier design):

# Текущая версия

<div class="image-container">
    iDryer x2
</div>
## Корпус

### Материал корпуса - фрезерованные PIR панели

<div class="image-container">
  <div class="custom-image">
    iDryer сборка контроллера сушилки филамента
  </div>
  <div class="custom-image">
    iDryer сборка контроллера сушилки филамента
  </div>
  <div class="custom-image">
    iDryer сборка контроллера сушилки филамента
  </div>
  <div class="custom-image">
    iDryer сборка контроллера сушилки филамента
  </div>
  <div class="custom-image">
    iDryer сборка контроллера сушилки филамента
  </div>
</div>

<div class="image-container">
  <div class="custom-image">
    iDryer сборка контроллера сушилки филамента
  </div>
  <div class="custom-image">
    iDryer сборка контроллера сушилки филамента
  </div>
  <div class="custom-image">
    iDryer сборка контроллера сушилки филамента
  </div>
  <div class="custom-image">
    iDryer сборка контроллера сушилки филамента
  </div>
  <div class="custom-image">
    iDryer сборка контроллера сушилки филамента
  </div>
</div>

<div class="image-container">
  <div class="custom-image">
    iDryer сборка контроллера сушилки филамента
  </div>
  <div class="custom-image">
    iDryer сборка контроллера сушилки филамента
  </div>
  <div class="custom-image">
    iDryer сборка контроллера сушилки филамента
  </div>
  <div class="custom-image">
    iDryer сборка контроллера сушилки филамента
  </div>
</div>

### Пол и катушкодержатели - металл
<div class="image-container">
  <div class="custom-image">
    iDryer сборка контроллера сушилки филамента
  </div>
  <div class="custom-image">
    iDryer сборка контроллера сушилки филамента
  </div>
  <div class="custom-image">
    iDryer сборка контроллера сушилки филамента
  </div>
  <!-- <div class="custom-image">
    <img src="https://raw.githubusercontent.com/pavluchenkor/iDryerProject/main/iDryer%20v2/Hardware/PIR%20Box%20v3/img/IMG_29129.jpg" alt="iDryer сборка контроллера сушилки филамента">
  </div> -->
</div>

### Материал печатных деталей - ABS или ABS CF

### Комплект поставки

Поставляется в виде KIT набора [KITx2](https://store.idryer.org/product/diy-%d1%81%d1%83%d1%88%d0%b8%d0%bb%d0%ba%d0%b0-%d1%84%d0%b8%d0%bb%d0%b0%d0%bc%d0%b5%d0%bd%d1%82%d0%b0-idryer-x2-%d0%bf%d0%be%d0%bb%d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)
, [KITx3](https://store.idryer.org/product/diy-%d1%81%d1%83%d1%88%d0%b8%d0%bb%d0%ba%d0%b0-%d1%84%d0%b8%d0%bb%d0%b0%d0%bc%d0%b5%d0%bd%d1%82%d0%b0-idryer-x3-%d0%bf%d0%be%d0%bb%d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)
, [KITx4](https://store.idryer.org/product/diy-%d1%81%d1%83%d1%88%d0%b8%d0%bb%d0%ba%d0%b0-%d1%84%d0%b8%d0%bb%d0%b0%d0%bc%d0%b5%d0%bd%d1%82%d0%b0-idryer-x4-%d0%bf%d0%be%d0%bb%d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)

[Видео сборки KIT набора](https://www.youtube.com/playlist?list=PLv8eJa-BRh3z09ve9bOKYYc3aWBMgUUt0)

### Детали для печати

!!! quote annotate "Детали в формате 3mf"

    :material-download:</i> **[iDryer_set1.3mf](CAD/iDryer_set1.3mf)**

    :material-download:</i> **[iDryer_set2.3mf](CAD/iDryer_set2.3mf)**
    
    :material-download:</i> **[LogoPlate.3mf](CAD/LogoPlate.3mf)**
    
    :material-download:</i> **[клипсы.3mf](CAD/клипсы.3mf)**
    
    :material-download:</i> **[панель_х2.3mf](CAD/панель_х2.3mf)**
    
    :material-download:</i> **[панель_х3.3mf](CAD/панель_х3.3mf)**
    
    :material-download:</i> **[панель_х4.3mf](CAD/панель_х4.3mf)**

### CAD

!!! quote annotate "Полная модель корпуса x2"

    :material-download:</i> **[Корпус PIR x2.stp](CAD/x2.stp)**

!!! quote annotate "Полная модель корпуса x3"

    :material-download:</i> **[Корпус PIR x3.stp](CAD/x3.stp)**

!!! quote annotate "Полная модель корпуса x4"

    :material-download:</i> **[Корпус PIR x4.stp](CAD/x4.stp)**

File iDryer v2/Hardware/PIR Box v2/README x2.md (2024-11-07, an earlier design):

# Сушилка филамента iDryer x2

## Особенности

- Количество катушек: 2
- Температура сушки: до 100С
- Контроль температуры нагревателя: да
- Контроль температуры воздуха в камере: да 
- Время сушки: не ограничено
- Принудительное проветривание: да
- Взвешивание филамента: да
- Пресеты: да
- Типы филамента: PLA, ABS, HIPS, PETG, SBS, Flex, PA6, PA12, PC, ABS, ASA, PP, POM и другие

<div class="image-container">
  <div class="custom-image">
    iDryer сборка корпуса
  </div>
  <div class="custom-image">
    iDryer сборка корпуса
  </div>
  <div class="custom-image">
    iDryer сборка корпуса
  </div>
</div>

!!! quote annotate "Полная модель корпуса"

    :material-download:</i> **[Корпус PIR x2.stp](CAD/Корпус PIR x2.stp)**

    Материал печатных деталей - ABS или ABS CF

!!! quote annotate "Раскрой"

    :material-download:</i> **[раскрой х2.pdf](https://raw.githubusercontent.com/pavluchenkor/iDryerProject/main/iDryer%20v2/Hardware/PIR%20Box%20v2/docs/раскрой%20х2.pdf)**

!!! warning annotate "Важно"

    Все детали находящиеся внутри корпуса печатаются из материалов выдерживающих нагревание 100С и выше.

    Воздуховод в подвале сушилки необходимо изолировать, теплоизоляция воздуховода в проекте x4 представлена для ознакомления, можно использовать в таком же виде или оклеить воздуховод любым теплоизоляционным материалом. Если этого не сделать, скорость прогрева будет снижена, а потребление электричества увеличится значительно!

[Contributing :material-file-edit:](https://github.com/pavluchenkor/iDryerProject/tree/main/iDryer%20v2/Hardware/PIR%20Box%20v2)

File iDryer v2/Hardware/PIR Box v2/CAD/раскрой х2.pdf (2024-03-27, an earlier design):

Результаты раскроя ••• Cutting 3 • Версия 1.50, ноябрь, 2008 • 27.03.2024 17:52:46 | Стр. 1

1.160 0.560

0.547 0.847 0.268 0.000

0.000 0.250

Лист №: 1 (1) Количество копий: 1 Материал: Silver Размер: 1.160 x 0.560 m.
Площадь листа: 0.650 sq.m. Количество деталей: 6 Отходы: 0.245 (37.7%) Маркированные остатки: 0.000 (0.0%) Длина реза: 0.000 m. Заметки:

### Детали

№ 4 300x250 Кол-во: 2 (2) боковина | № 5 300x208 Кол-во: 1 (1) зад
№ 3 268x250 Кол-во: 1 (1) верх | № 2 268x297 Кол-во: 1 (1) дверь

### № 1 208x220 Кол-во: 1 (1) пол

4

300 250

боковина

4

300 250

боковина

5

300 208

зад

3

250 268 | верх

2

297 268

дверь | 1
220 208

пол

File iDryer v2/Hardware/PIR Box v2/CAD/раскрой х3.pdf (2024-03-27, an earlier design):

Результаты раскроя ••• Cutting 3 • Версия 1.50, ноябрь, 2008 • 27.03.2024 17:50:13 | Стр. 1

1.160 0.560

0.250 0.300 0.000 250 300 боковина | 368 297 2 дверь | 308 300 зад
368 250 3 верх | 300 250 4 боковина | 308 220 1 пол

0.000 0.618

Лист №: 1 (1) Количество копий: 1 Материал: Silver Размер: 1.160 x 0.560 m.
Площадь листа: 0.650 sq.m. Количество деталей: 6 Отходы: 0.138 (21.3%) Маркированные остатки: 0.000 (0.0%) Длина реза: 0.000 m. Заметки:

### Детали

№ 2 368x297 Кол-во: 1 (1) дверь | № 3 368x250 Кол-во: 1 (1) верх
№ 4 300x250 Кол-во: 2 (2) боковина | № 5 300x308 Кол-во: 1 (1) зад

### № 1 308x220 Кол-во: 1 (1) пол

4

5

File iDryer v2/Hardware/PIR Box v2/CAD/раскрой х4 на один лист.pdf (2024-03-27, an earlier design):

Результаты раскроя ••• Cutting 3 • Версия 1.50, ноябрь, 2008 • 27.03.2024 17:57:12 | Стр. 1

1.160 0.560 0.300 0.000

0.000 | 0.250 | 0.718

Лист №: 1 (1) Количество копий: 1 Материал: Silver Размер: 1.160 x 0.560 m.
Площадь листа: 0.650 sq.m. Количество деталей: 7 Отходы: 0.031 (4.8%) Маркированные остатки: 0.000 (0.0%) Длина реза: 0.000 m. Заметки:

### Детали

№ 6 260x250 Кол-во: 1 (1) боковина 2 склеить | № 4 300x250 Кол-во: 1 (1) боковина
№ 1 408x220 Кол-во: 1 (1) пол | № 3 468x250 Кол-во: 1 (1) верх
№ 5 300x408 Кол-во: 1 (1) зад | № 2 468x297 Кол-во: 1 (1) дверь

### № 7 40x250 Кол-во: 1 (1) боковина 1 склеить

6

4

250 300 боковина | 468 297 2 дверь | 408 300 зад
250 260 боковина 2 склеить | 468 250 3 верх | 408 220 1 пол

5

боковина 1 склеить18

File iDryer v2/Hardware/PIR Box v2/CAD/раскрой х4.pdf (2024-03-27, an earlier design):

Результаты раскроя ••• Cutting 3 • Версия 1.50, ноябрь, 2008 • 27.03.2024 17:42:38 | Стр. 1

1.160 0.560

0.250 0.300 0.000 250 300 | 468 297 2 | 408 300 5
408 220 1 | 468 250 3

0.000 0.718

Лист №: 1 (1) Количество копий: 1 Материал: Silver Размер: 1.160 x 0.560 m.
Площадь листа: 0.650 sq.m. Количество деталей: 5 Отходы: 0.106 (16.4%) Маркированные остатки: 0.000 (0.0%) Длина реза: 0.000 m. Заметки:

### Детали

№ 2 468x297 Кол-во: 1 (1) | № 1 408x220 Кол-во: 1 (1)
№ 3 468x250 Кол-во: 1 (1) | № 4 300x250 Кол-во: 1 (1)

### № 5 300x408 Кол-во: 1 (1)

4

Результаты раскроя ••• Cutting 3 • Версия 1.50, ноябрь, 2008 • 27.03.2024 17:42:38 | Стр. 2

1.160 0.560 0.000

0.000

Лист №: 1 (2) Количество копий: 1 Материал: Silver Размер: 1.160 x 0.560 m.
Площадь листа: 0.650 sq.m. Количество деталей: 1 Отходы: 0.575 (88.5%) Маркированные остатки: 0.000 (0.0%) Длина реза: 0.000 m. Заметки:

### Детали № 4 300x250 Кол-во: 1 (1)

4

250 300

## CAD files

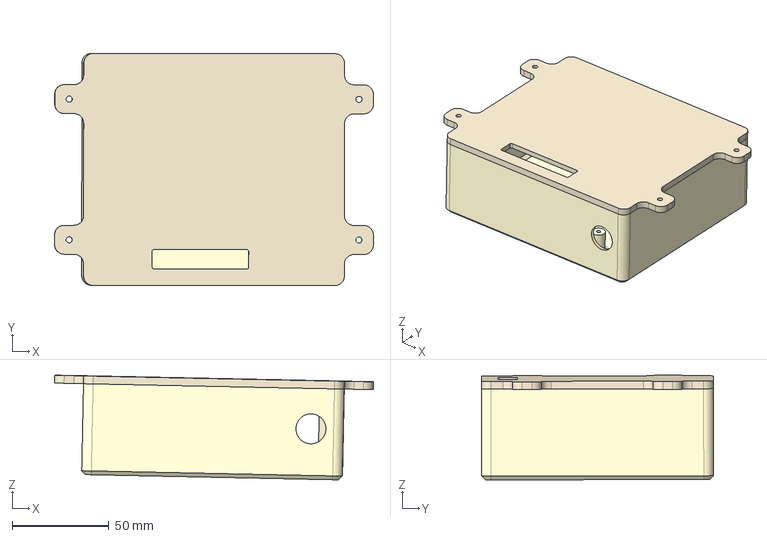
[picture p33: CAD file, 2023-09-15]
iDryer v2/Hardware/PCB Case/CAD/Assembly_ebox.stp
165.0 x 120.1 x 54.2 mm
box_lower

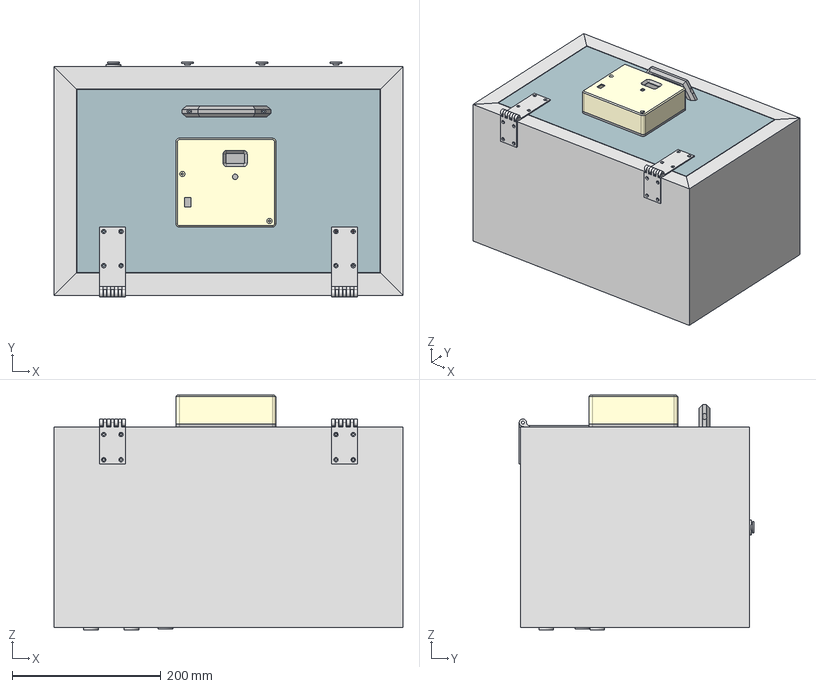
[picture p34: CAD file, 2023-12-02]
iDryer v2/Hardware/PIR Box/CAD/PIR_box_assembly.stp
470.0 x 316.0 x 316.0 mm
Платформа x 4
Датчик x 3
Bearing 619/4-2Z GB/T 276-94 x 16
Деталь17 x 4
Ось x 4
Ось_1 x 4
Катушка мелкая x 4
Вал2 x 8
FD plast spool x 4
Датчик_1
Узкий левая стенка
Узкий правая стенка
Узкий дно
Узкий верх
Узкий зад
Узкая дверь
Петля1
Петля2
подставка под весы алюминий
ISO 7046-1 - M5 x 25 - 4.8 - H x 4
Нагреватель 2 4В
7525_MIR
воздуховод нагревателя 7530
Дюбель м4 x 2
Дюбель м3 x 12
Петля1_MIR
Петля2_MIR
Ручка
box_lower
кольцо для филамента x 4
ответка дюбеля м3

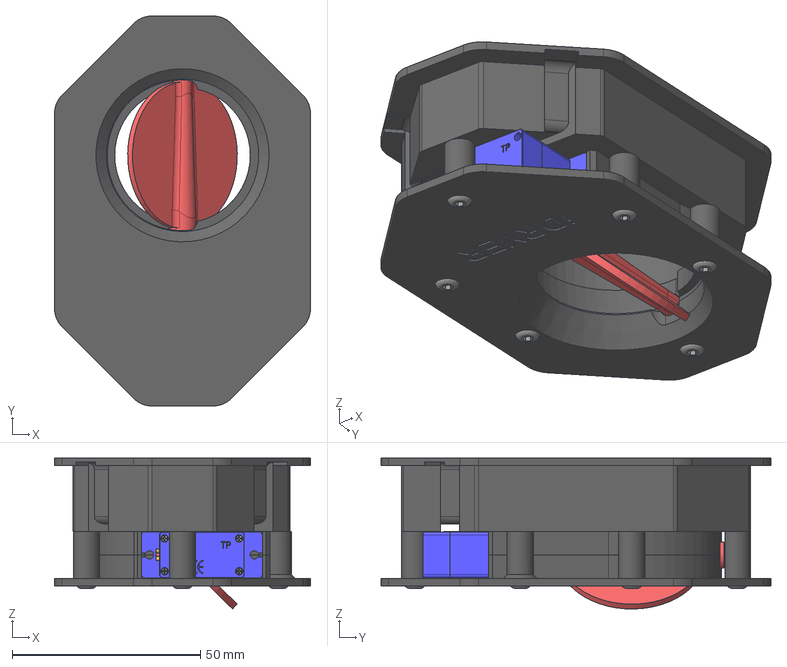
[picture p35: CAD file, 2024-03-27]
iDryer v2/Hardware/air damper/CAD/Заслонка Финал.stp
68.0 x 103.6 x 40.1 mm
SG90 - Micro Servo 9g - Tower Pro.1_Pea
SG90 - Micro Servo 9g - Tower Pro.6_BS EN ISO 7045 - M2 x 4 - Z - 4S
Корпус заслонки
лепесток заслонки
дифузор заслонки внут
ISO 7380-1 - M3 x 20 x 6
ISO 7380-1 - M3 x 10 x 3

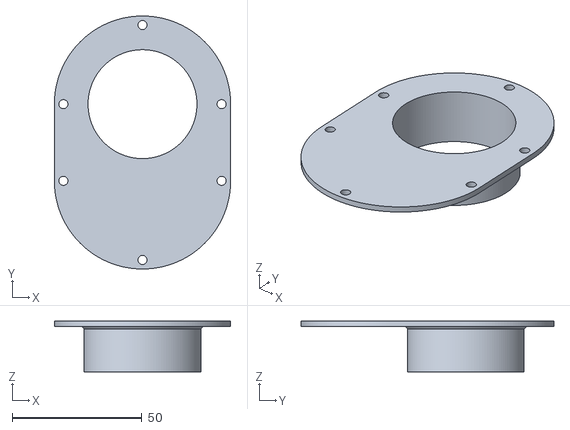
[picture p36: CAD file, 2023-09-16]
iDryer v2/Hardware/air damper/STL/air_damper_diffuser.stl
68.0 x 97.6 x 19.5

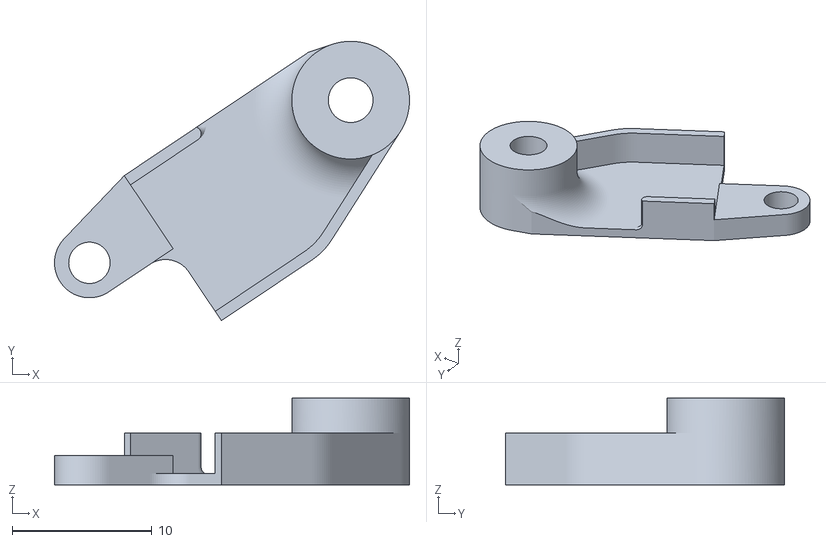
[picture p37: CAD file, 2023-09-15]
iDryer v2/Hardware/Heater/7530-7525/CAD/Крепление бме280.stl
25.4 x 20.0 x 6.21

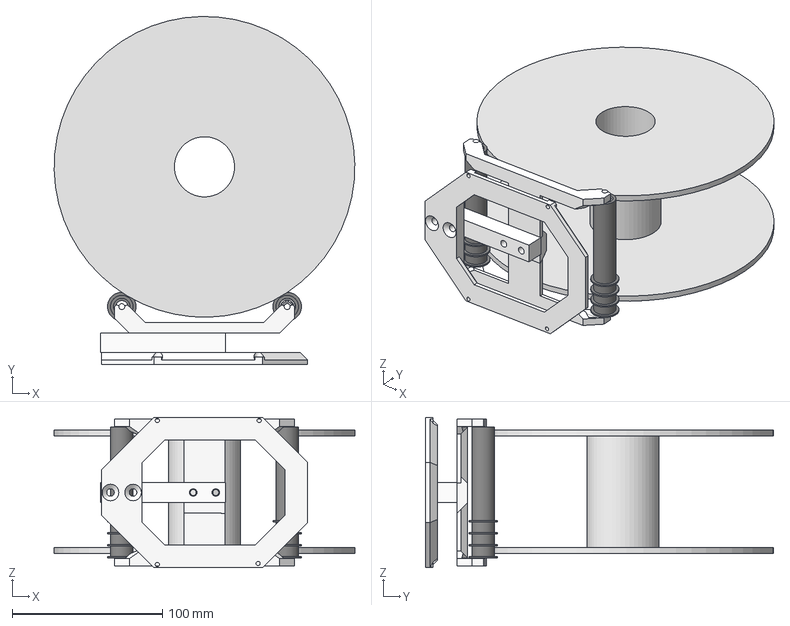
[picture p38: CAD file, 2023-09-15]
iDryer v2/Hardware/Scale module/CAD/for 3D printing/Весы узкие.stp
199.9 x 231.4 x 100.0 mm
Платформа
Датчик
Деталь17
Ось
Ось_1
Катушка мелкая
Rolling bearing 70000B S719/4 GB/T 292-94 x 2
Вал2 x 2

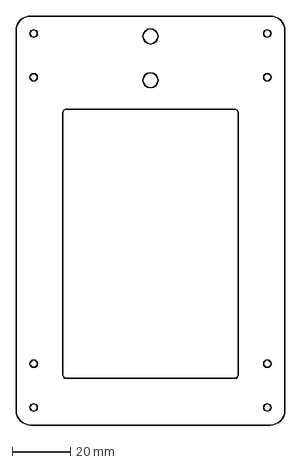
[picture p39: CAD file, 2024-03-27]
iDryer v2/Hardware/Scale module/CAD/for cutting metal/Base_Single_v1_2.DXF
92.0 x 140.0 mm

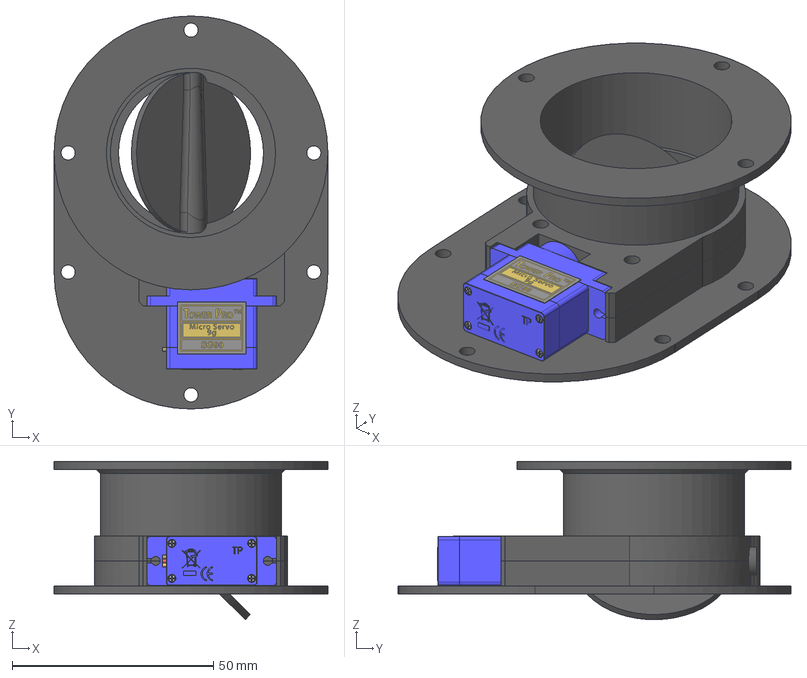
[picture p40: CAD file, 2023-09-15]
iDryer v2/Hardware/air damper/CAD/air damper.stp
68.0 x 97.6 x 39.3 mm
SG90 - Micro Servo 9g - Tower Pro.1_Pea
SG90 - Micro Servo 9g - Tower Pro.6_BS EN ISO 7045 - M2 x 4 - Z - 4S
Корпус заслонки
лепесток заслонки
дифузор заслонки внут

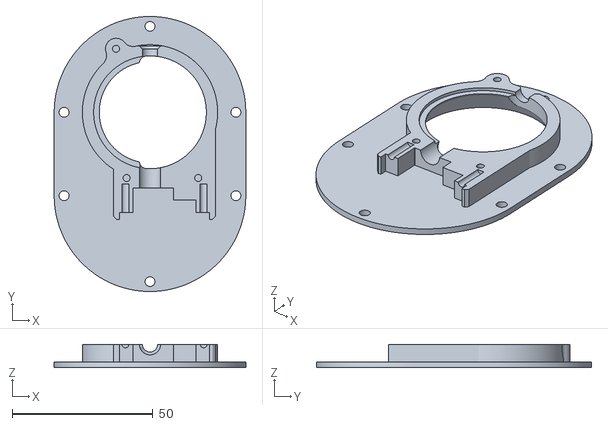
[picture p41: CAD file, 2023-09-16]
iDryer v2/Hardware/air damper/STL/air_damper_front.stl
68.0 x 97.6 x 8.25

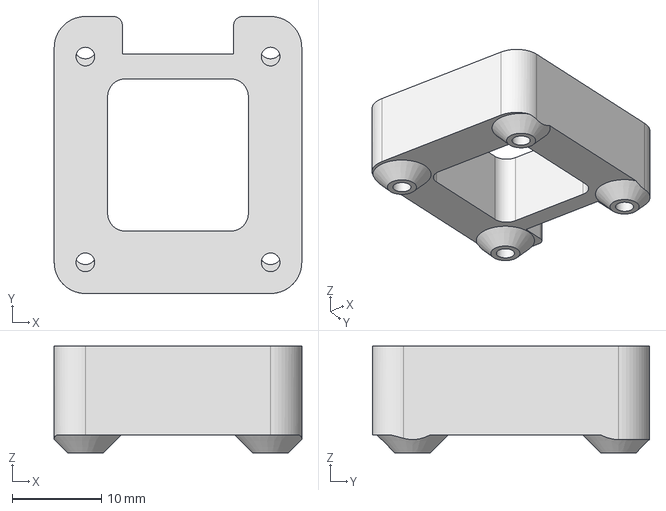
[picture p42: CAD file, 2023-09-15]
iDryer v2/Hardware/PCB Case/CAD/screen_stand.stp
27.8 x 31.1 x 12.0 mm

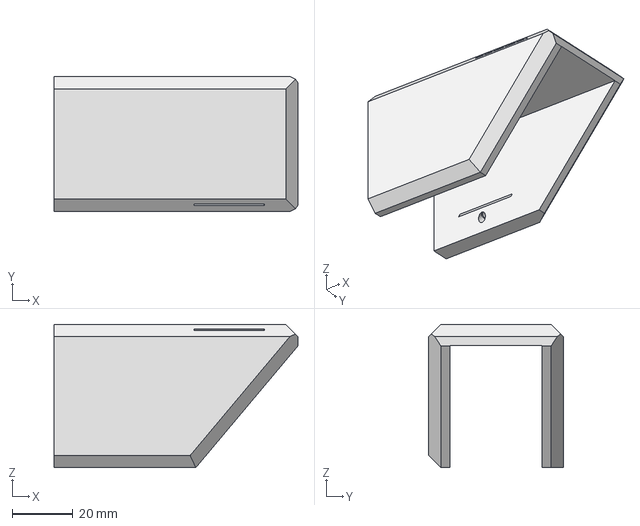
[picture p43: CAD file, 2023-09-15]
iDryer v2/Hardware/PIR Box/CAD/Оснастка ножа.stp
80.0 x 44.2 x 47.0 mm

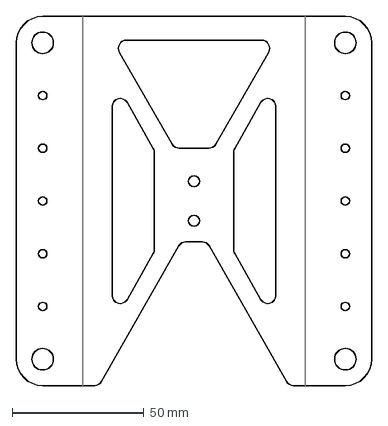
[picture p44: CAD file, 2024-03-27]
iDryer v2/Hardware/Scale module/CAD/for cutting metal/Rollers_Holder_v1_3.DXF
134.8 x 140.0 mm

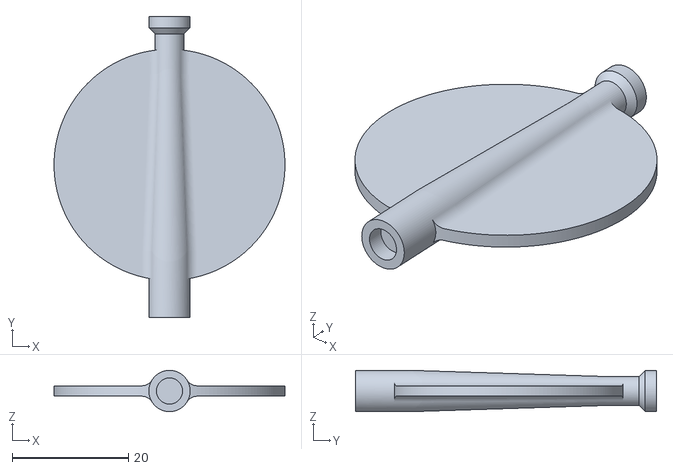
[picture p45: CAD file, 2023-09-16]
iDryer v2/Hardware/air damper/STL/air_damper_flap.stl
39.7 x 51.7 x 7.10

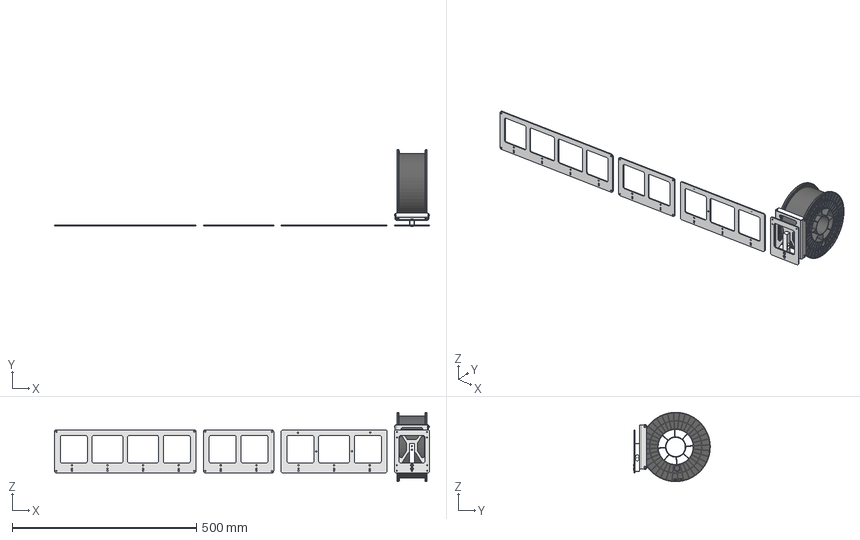
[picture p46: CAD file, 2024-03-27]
iDryer v2/Hardware/Scale module/CAD/for cutting metal/Катушкодержатель гибка финал.stp
1016.8 x 207.8 x 187.9 mm
Основание под одну катушку
FD plast spool
Ролик 623 x 2
Узкие весы гибка 623
Датчик
skf_bearing_623_2_1 x 4
ISO 7380-1 - M4 x 12 x 2
ISO 7380-1 - M3 x 8 x 4
ISO 10642 - M4 x 12 x 2
основание весов
Основание весов 2 кат
основание весов 3 кат

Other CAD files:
iDryer v2/Hardware/air damper/STL/air_damper_back.stl
iDryer v2/Hardware/Scale module/CAD/for cutting metal/SpoolHolderWeightModule_v1_3_2.STEP
iDryer v2/Hardware/Scale module/CAD/for cutting metal/Sasha.STEP
iDryer v2/Hardware/Scale module/CAD/for cutting metal/Модуль_катушкодержателей_с_весами_3_ячейки.igs
iDryer v2/Hardware/PIR Box v3/CAD/LogoPlate.3mf
iDryer v2/Hardware/PIR Box v3/CAD/iDryer_set1.3mf
iDryer v2/Hardware/PIR Box v3/CAD/iDryer_set2.3mf
iDryer v2/Hardware/PIR Box v3/CAD/клипсы.3mf
iDryer v2/Hardware/PIR Box v3/CAD/панель_х2.3mf
iDryer v2/Hardware/PIR Box v3/CAD/панель_х3.3mf
iDryer v2/Hardware/PIR Box v3/CAD/панель_х4.3mf
iDryer v2/Hardware/Scale module/CAD/for cutting metal/SpoolHolderWeightModule.STEP

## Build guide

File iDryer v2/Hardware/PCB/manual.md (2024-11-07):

# Инструкция по сборке контроллера r2.1

Выполняя простую последовательность действий, примерно через 40-60 минут можно получить полностью собранное устройство.
Из инструментов и принадлежностей потребуется:

- паяльник
- припой
- паяльная паста/канифоль
- бокорезы/кусачки
- спирт для промывки платы после пайки

!!! warning "Перед сборкой необходимо выставить напряжение 5.1В на выходе преобразователя MP1584 и перепаять резистор выбора частоты обновления на hx711"
    <div class="image-container">
      <div class="custom-image">
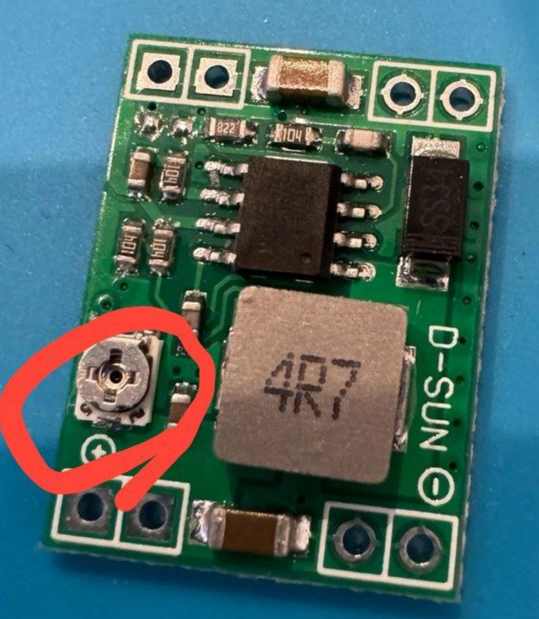
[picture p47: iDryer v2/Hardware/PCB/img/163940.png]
iDryer сборка контроллера сушилки филамента
          
      </div>
      <div class="custom-image">
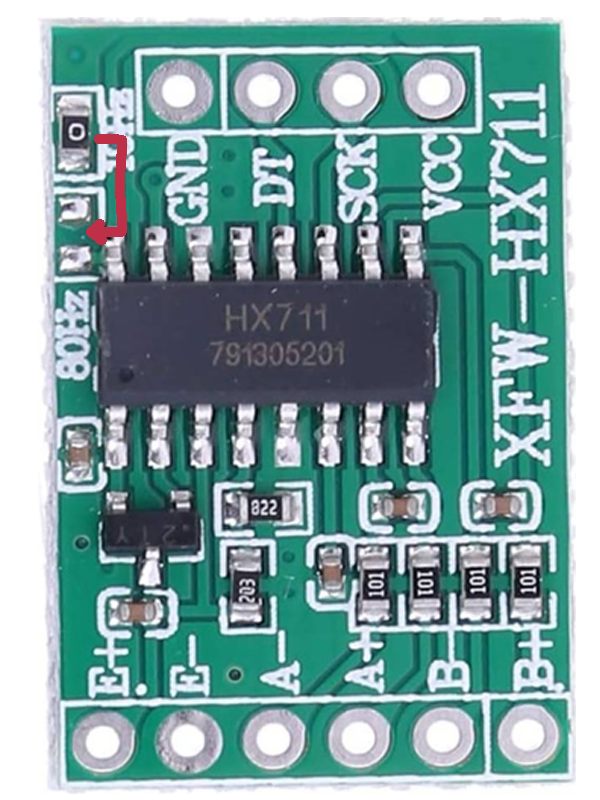
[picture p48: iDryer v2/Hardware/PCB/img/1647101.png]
iDryer сборка контроллера сушилки филамента
        
      </div>
    </div>

###  Последовательность сборки

<div class="image-container">
  <div class="custom-image">
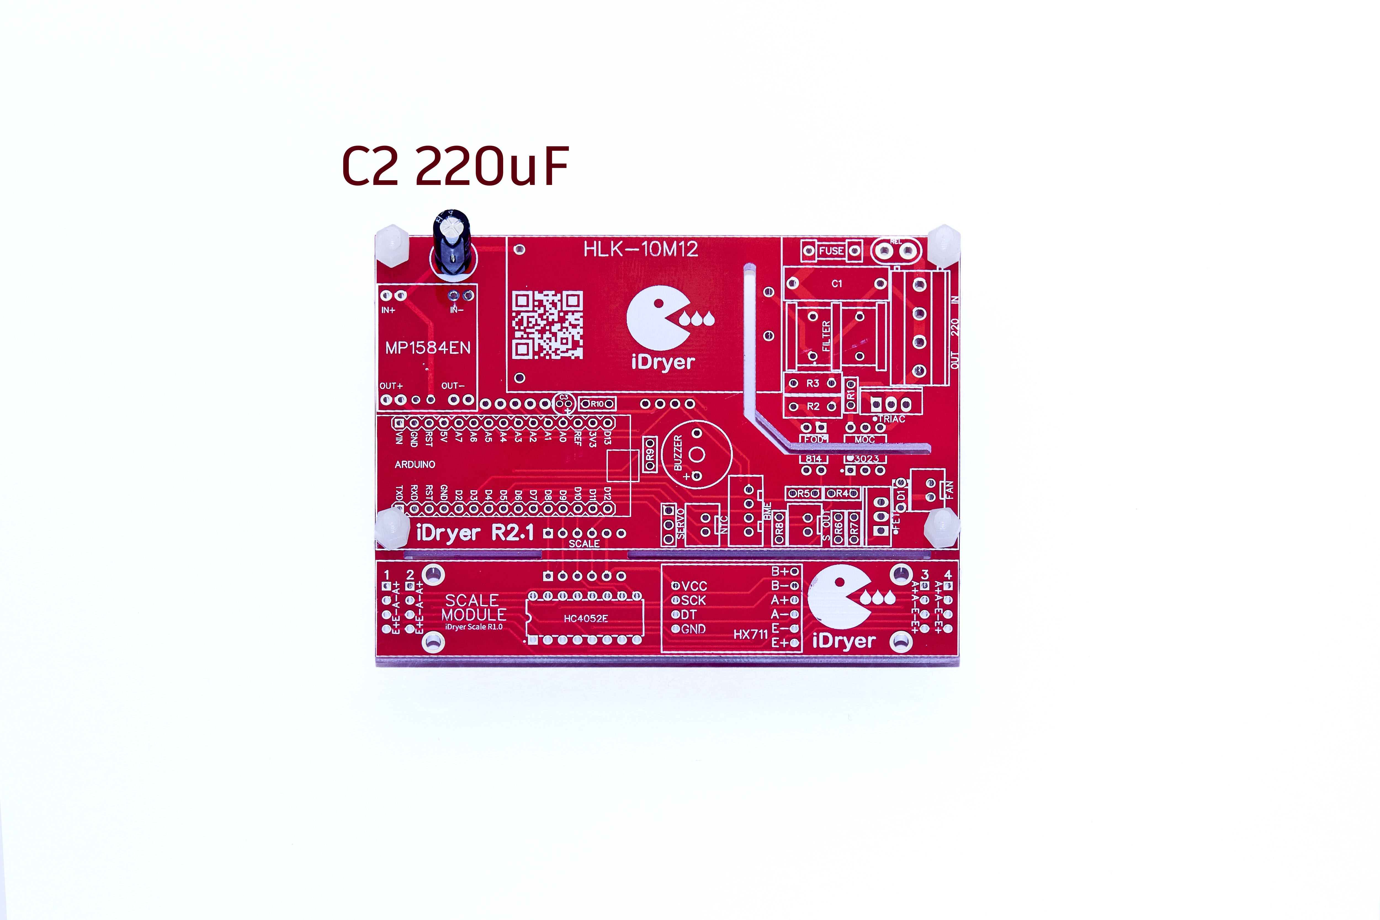
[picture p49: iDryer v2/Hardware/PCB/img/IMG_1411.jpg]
iDryer сборка контроллера сушилки филамента
    
  </div>
  <div class="custom-image">
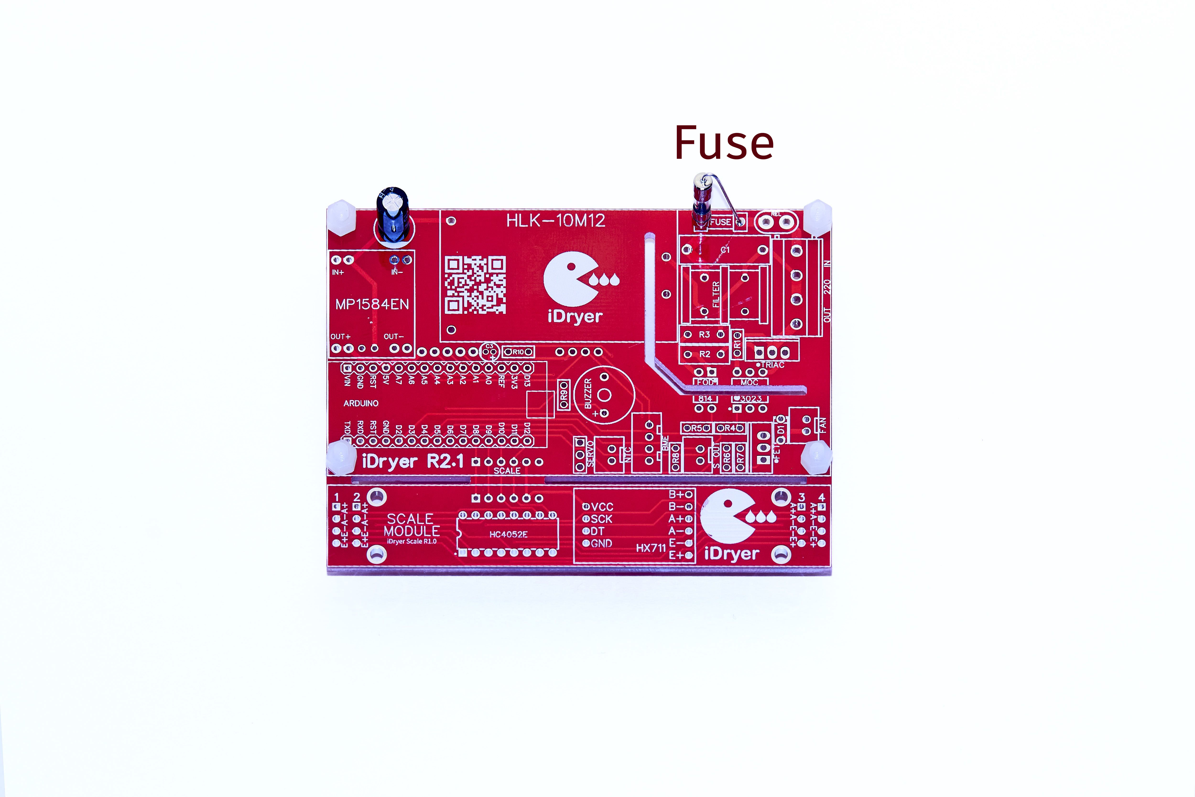
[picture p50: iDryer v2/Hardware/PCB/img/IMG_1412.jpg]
iDryer сборка контроллера сушилки филамента
    
  </div>
  <div class="custom-image">
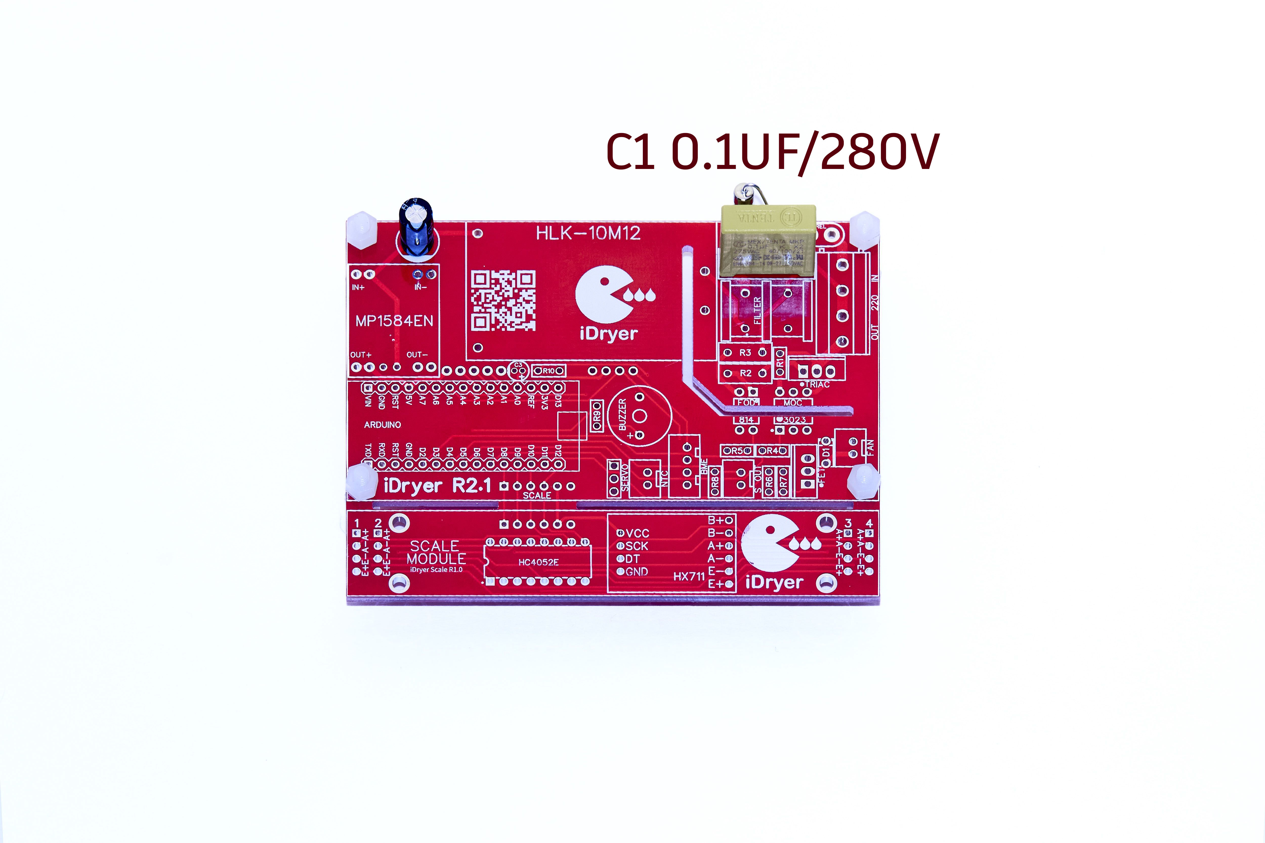
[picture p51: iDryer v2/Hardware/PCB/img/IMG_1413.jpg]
iDryer сборка контроллера сушилки филамента
    
  </div>
</div>

<div class="image-container">
  <div class="custom-image">
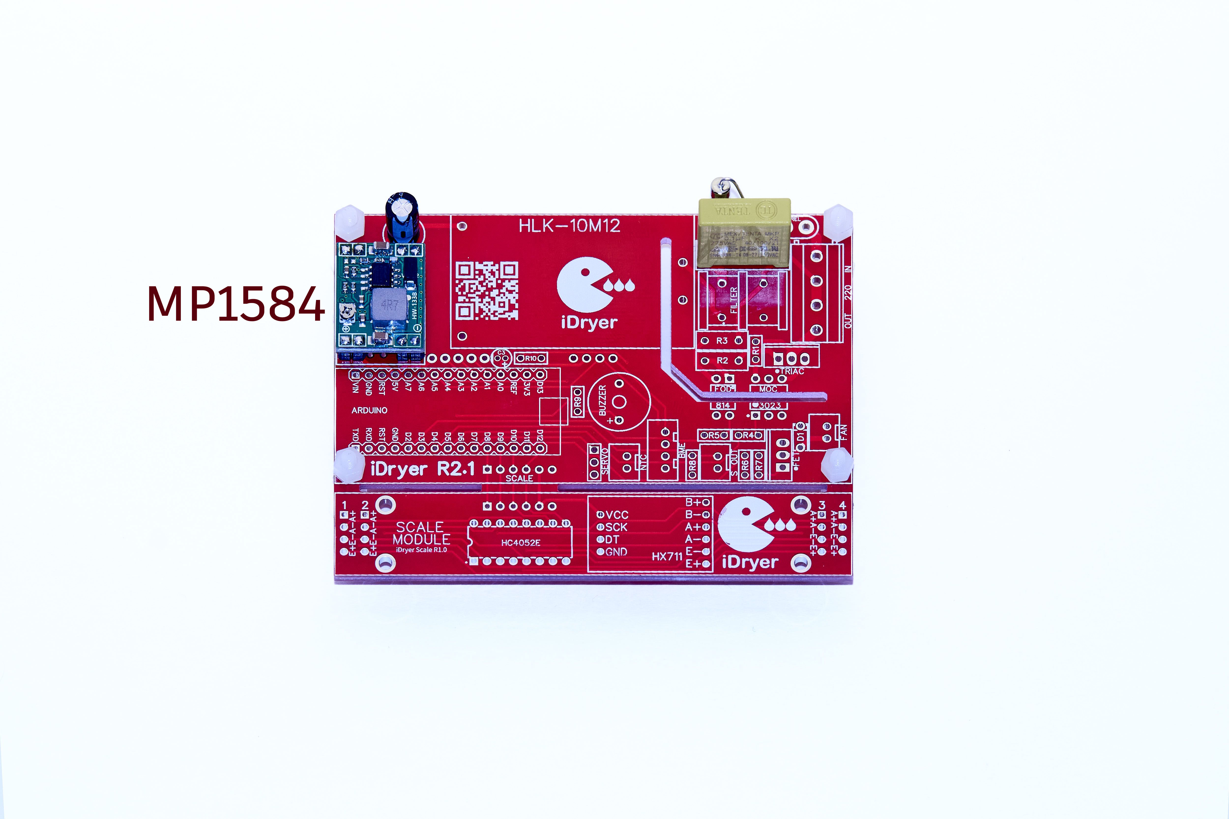
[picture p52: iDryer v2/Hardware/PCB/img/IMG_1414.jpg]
iDryer сборка контроллера сушилки филамента
    
  </div>
  <div class="custom-image">
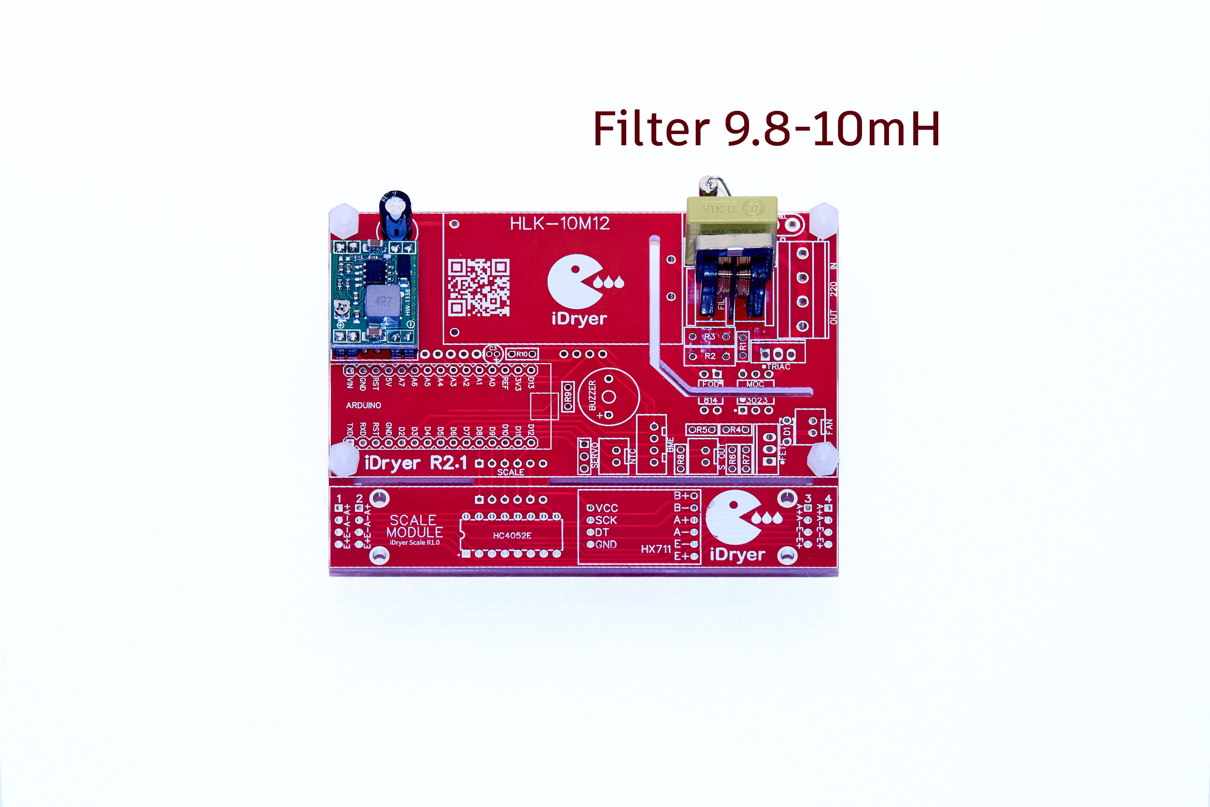
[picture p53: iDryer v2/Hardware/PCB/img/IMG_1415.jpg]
iDryer сборка контроллера сушилки филамента
    
  </div>
  <div class="custom-image">
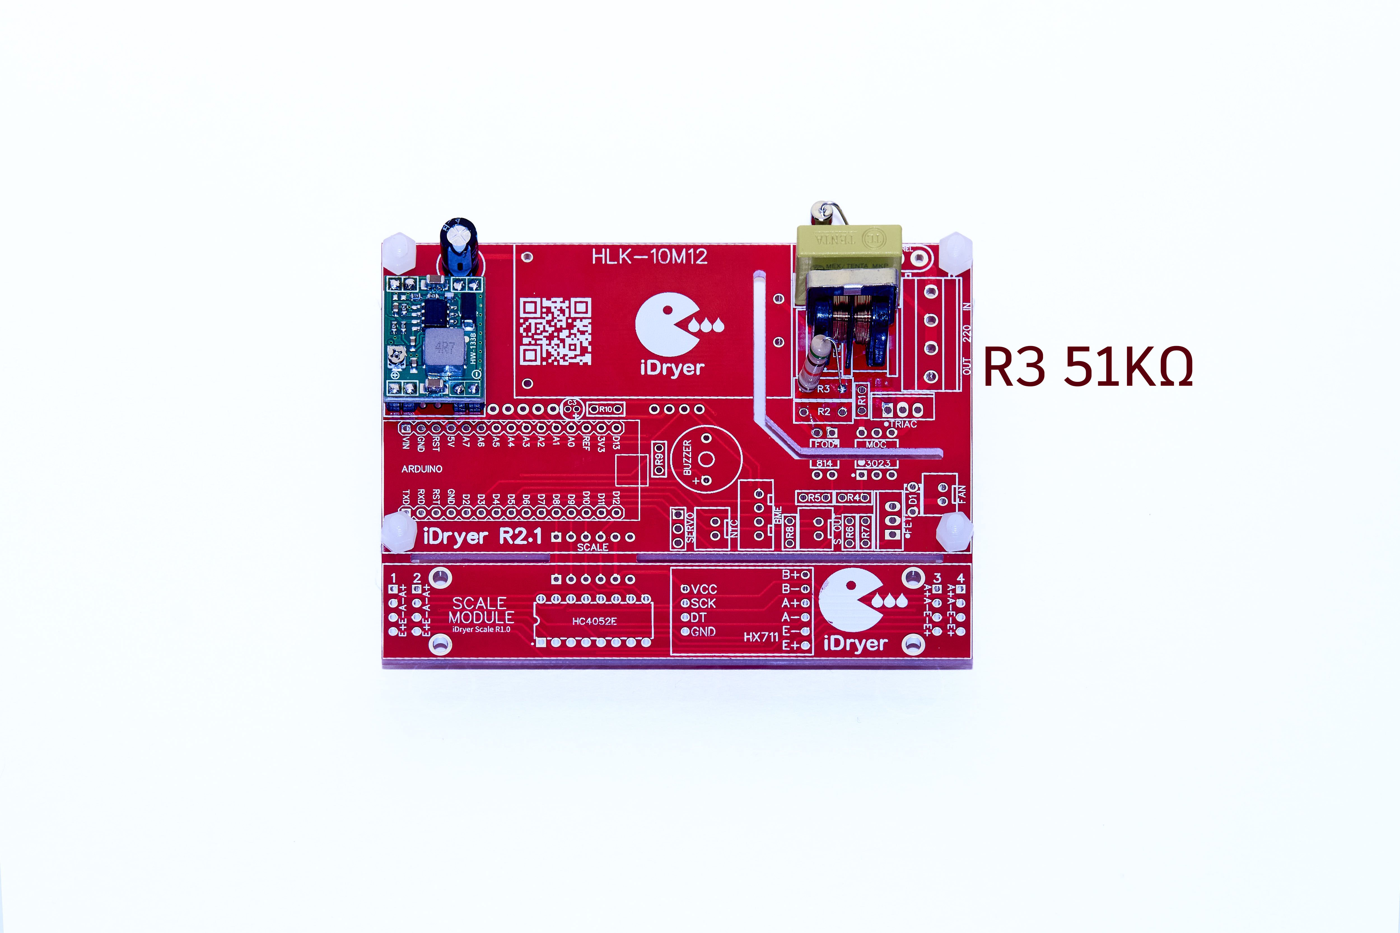
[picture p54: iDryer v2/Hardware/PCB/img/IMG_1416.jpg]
iDryer сборка контроллера сушилки филамента
    
  </div>
</div>

<div class="image-container">
  <div class="custom-image">
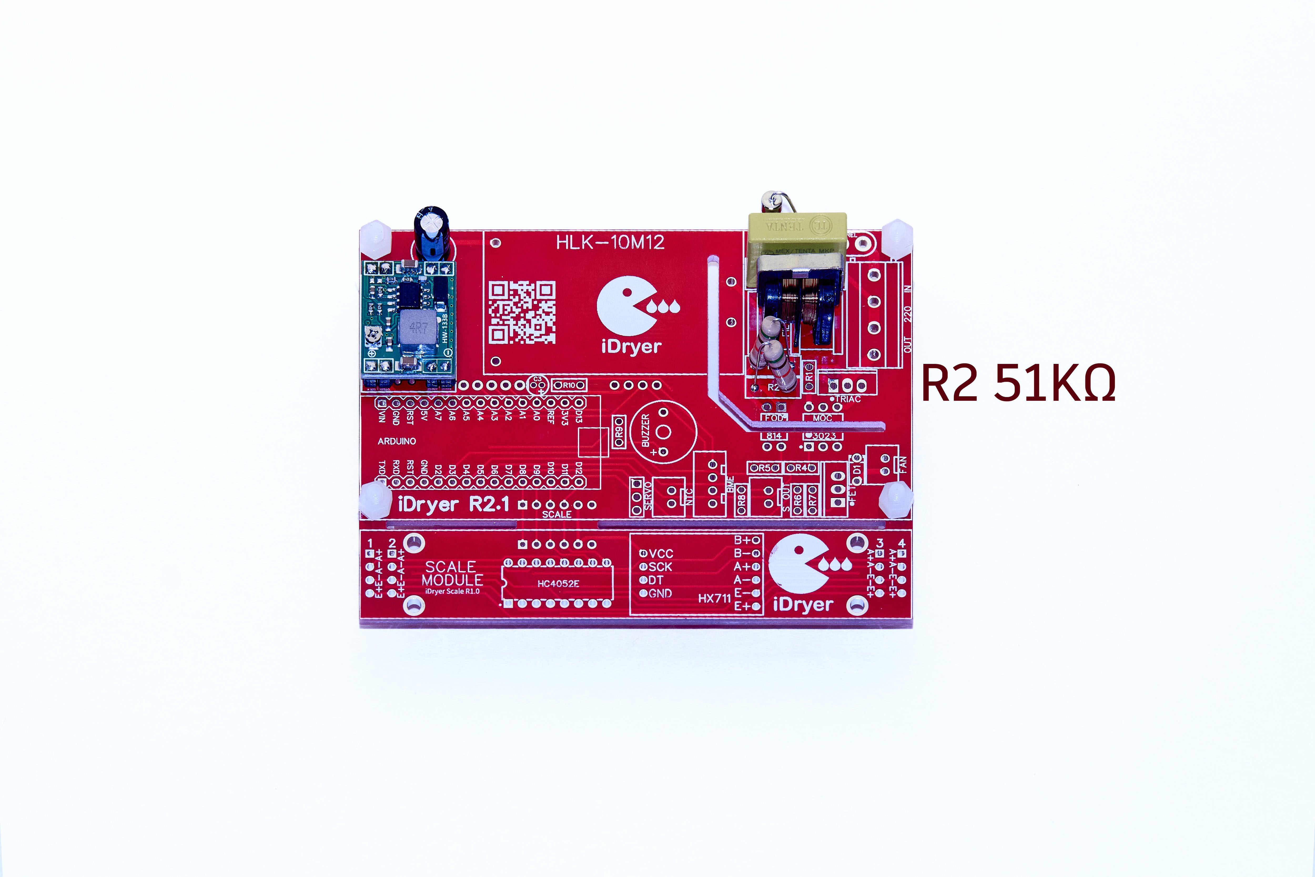
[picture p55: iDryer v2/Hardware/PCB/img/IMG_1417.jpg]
iDryer сборка контроллера сушилки филамента
    
  </div>
  <div class="custom-image">
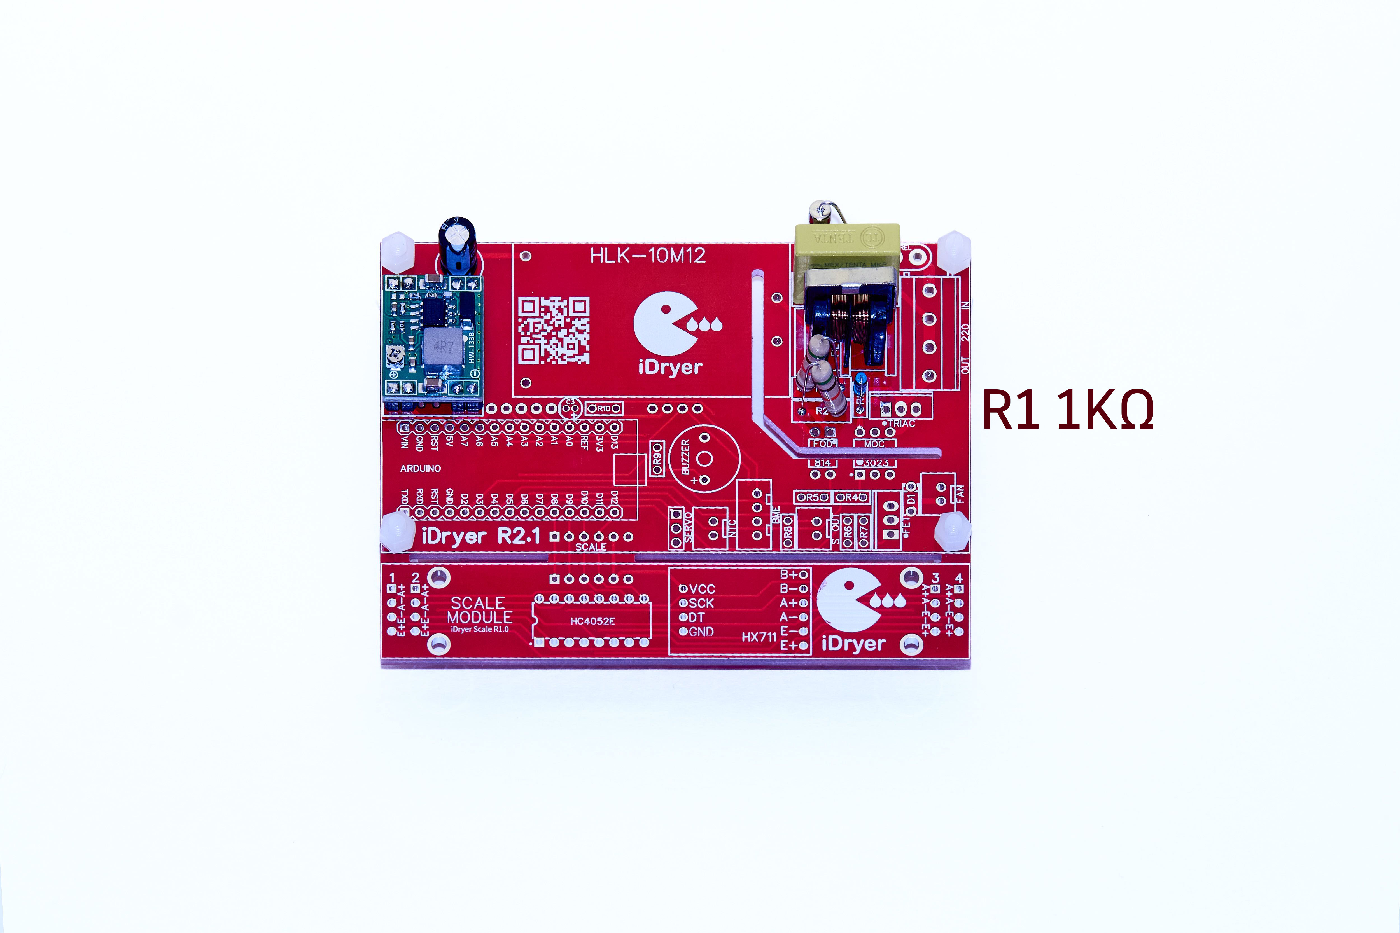
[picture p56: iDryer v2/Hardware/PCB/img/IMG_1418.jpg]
iDryer сборка контроллера сушилки филамента
    
  </div>
  <div class="custom-image">
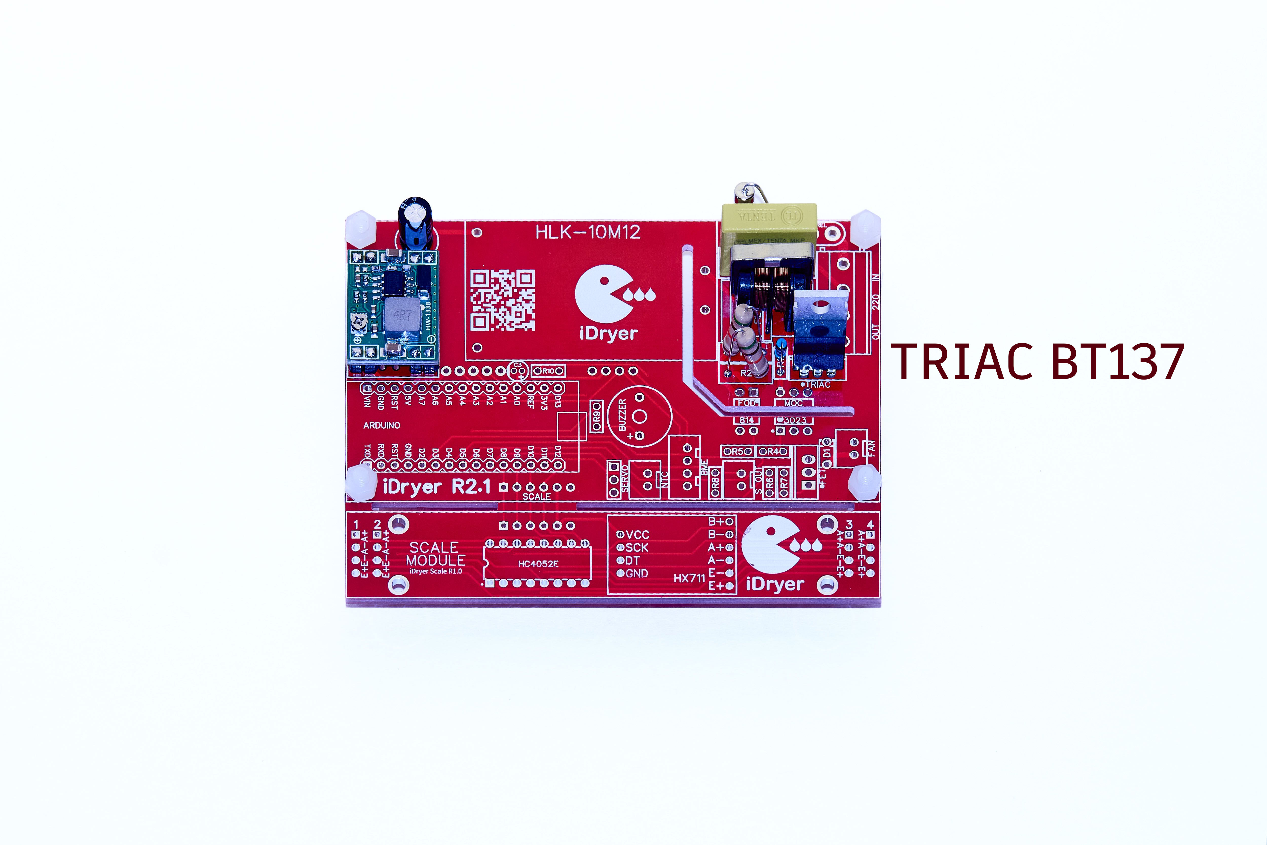
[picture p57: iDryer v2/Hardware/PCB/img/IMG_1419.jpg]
iDryer сборка контроллера сушилки филамента
    
  </div>
</div>

<div class="image-container">
  <div class="custom-image">
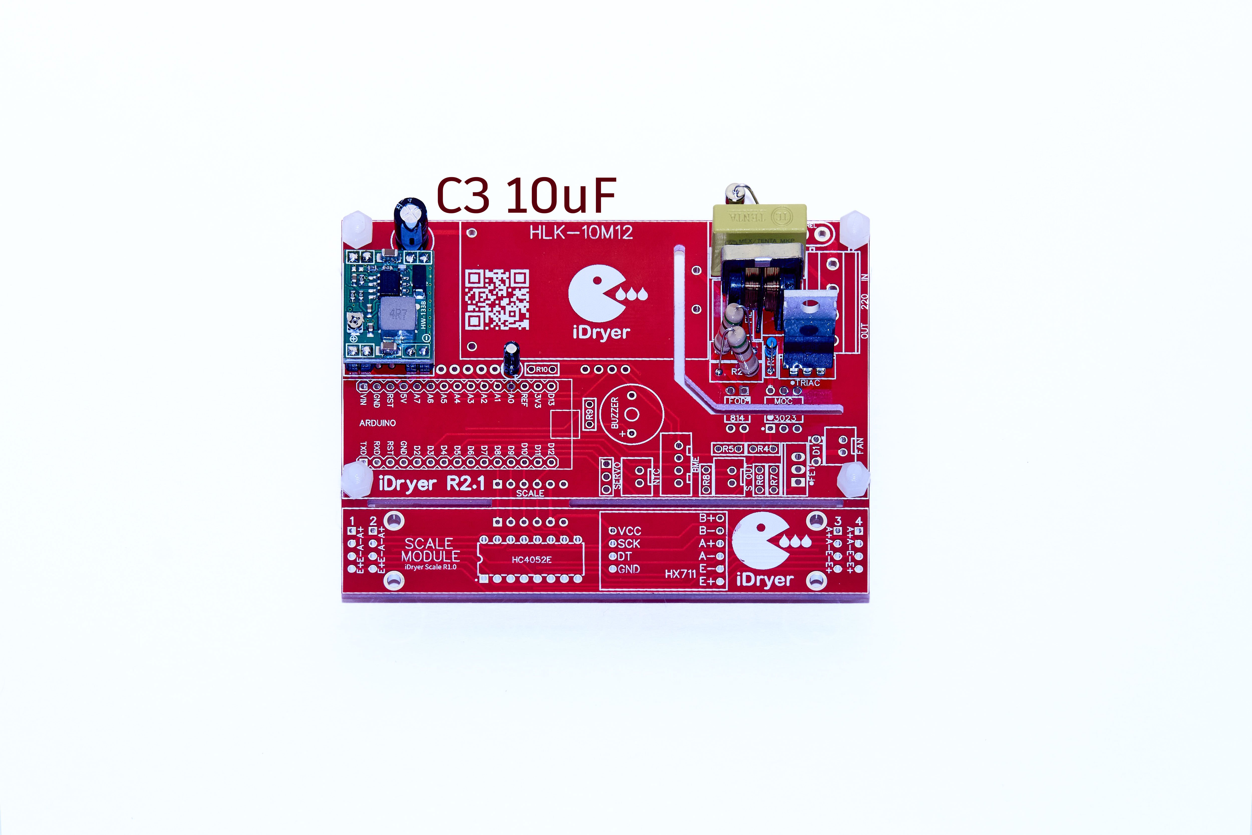
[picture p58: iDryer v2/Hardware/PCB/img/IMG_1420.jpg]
iDryer сборка контроллера сушилки филамента
    
  </div>
  <div class="custom-image">
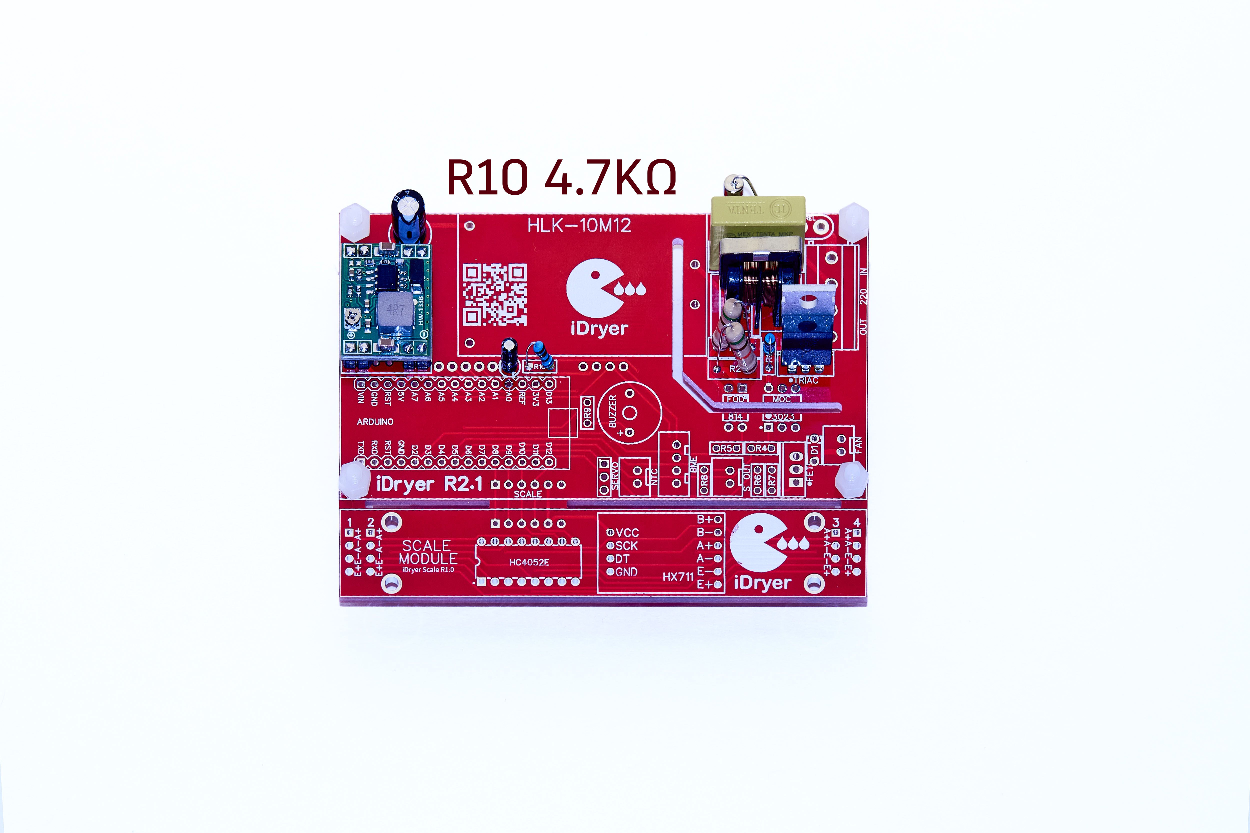
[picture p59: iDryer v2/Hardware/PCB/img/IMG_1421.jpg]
iDryer сборка контроллера сушилки филамента
    
  </div>
  <div class="custom-image">
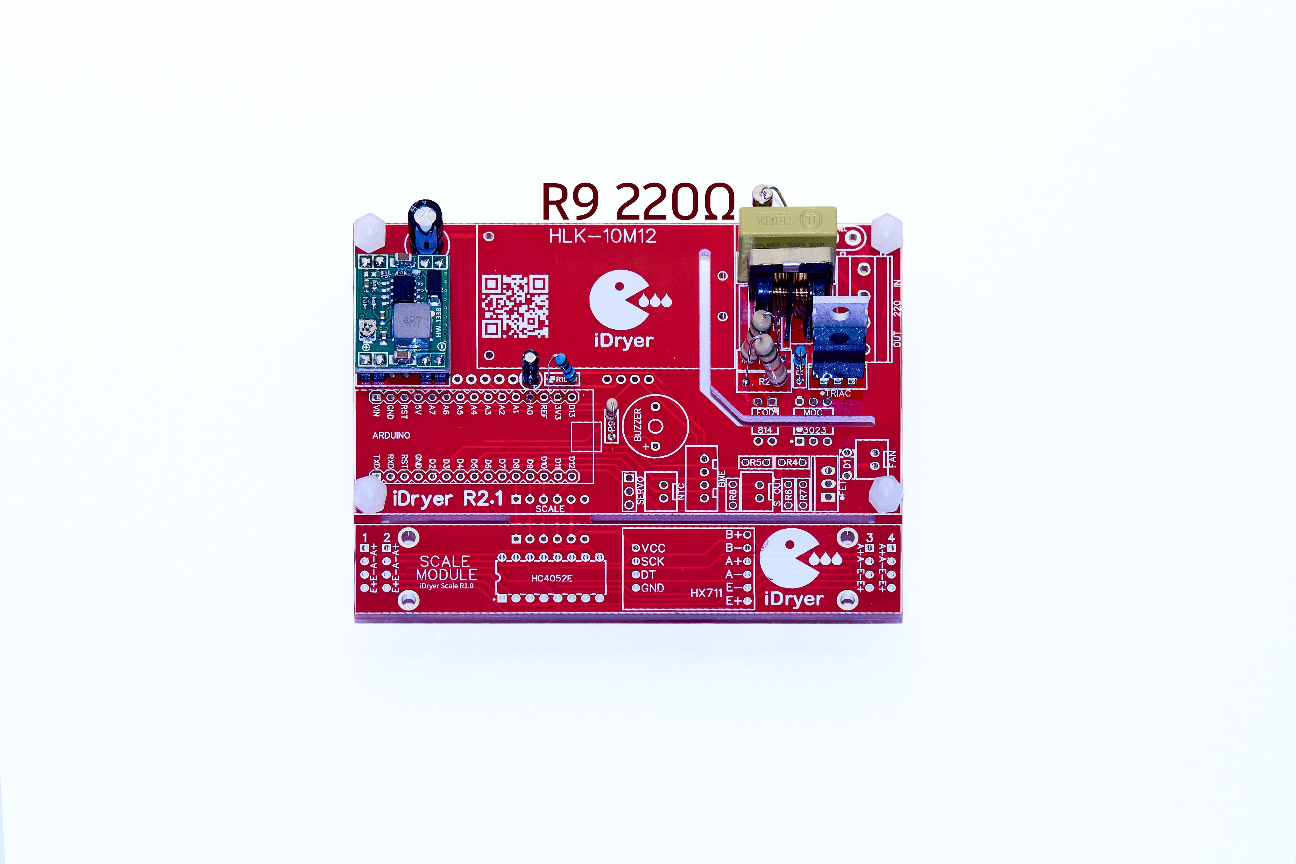
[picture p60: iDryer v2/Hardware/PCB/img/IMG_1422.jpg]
iDryer сборка контроллера сушилки филамента
    
  </div>
</div>

<div class="image-container">
  <div class="custom-image">
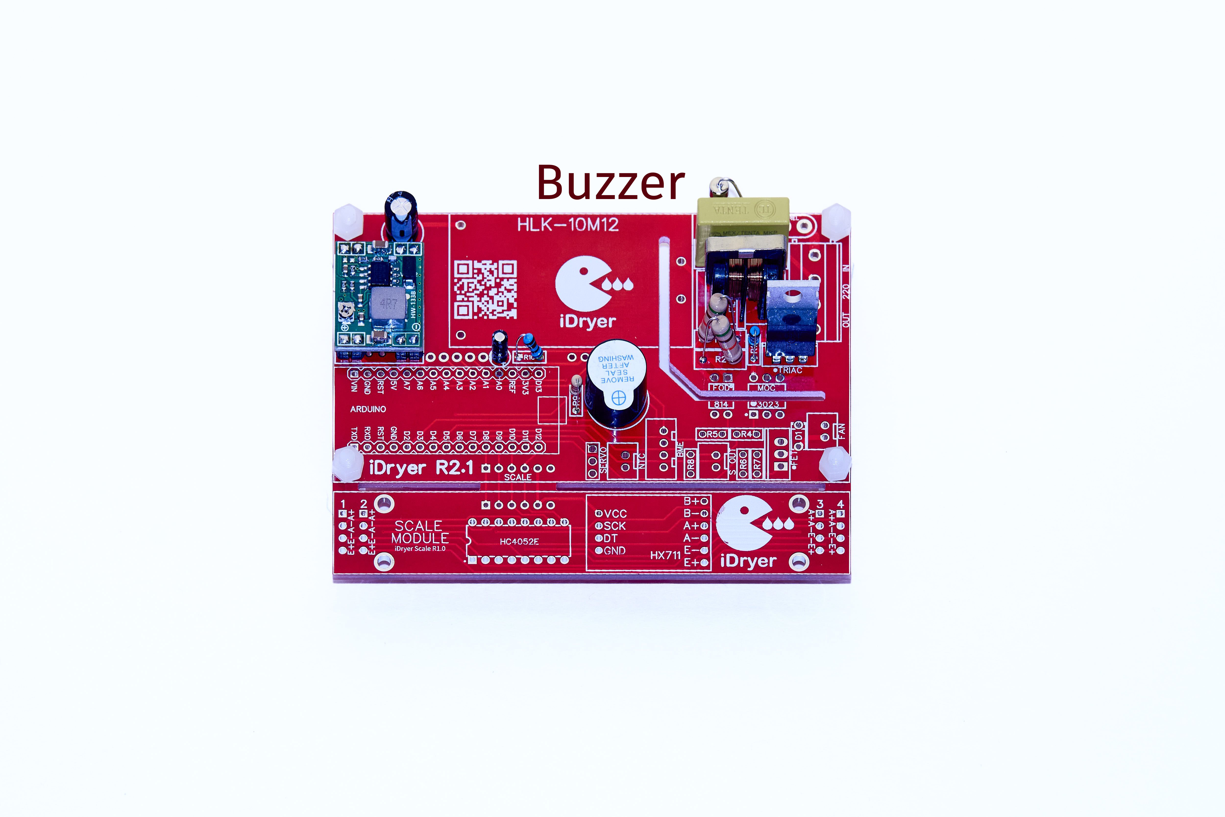
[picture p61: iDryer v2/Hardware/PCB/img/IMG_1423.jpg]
iDryer сборка контроллера сушилки филамента
    
  </div>
  <div class="custom-image">
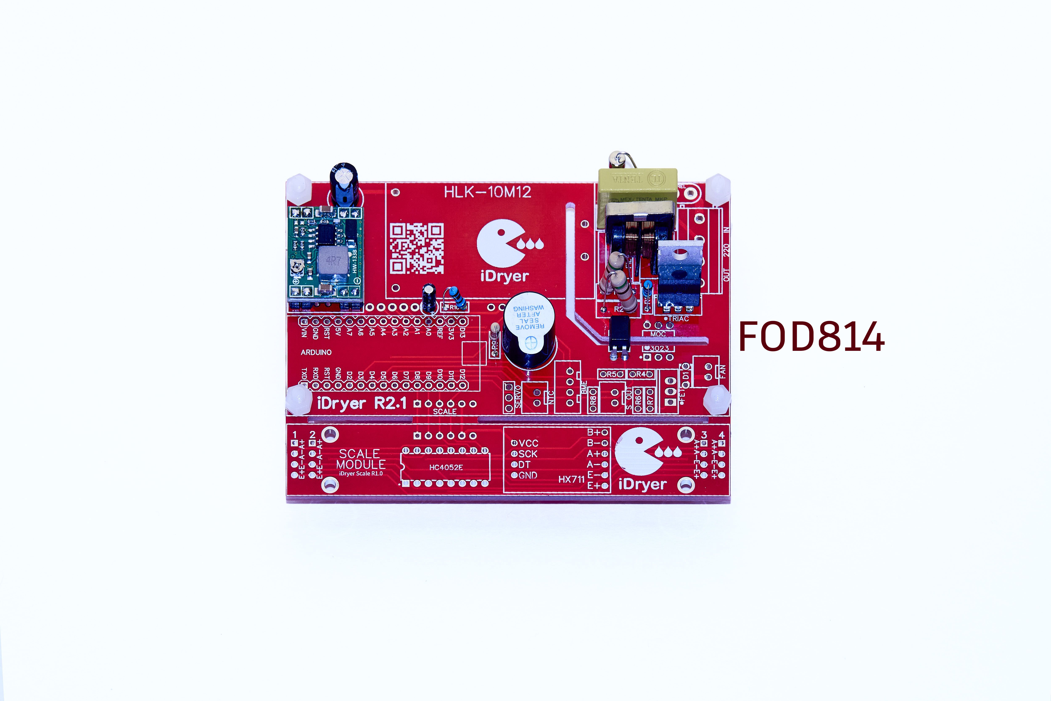
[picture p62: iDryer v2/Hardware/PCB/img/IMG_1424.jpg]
iDryer сборка контроллера сушилки филамента
    
  </div>
  <div class="custom-image">
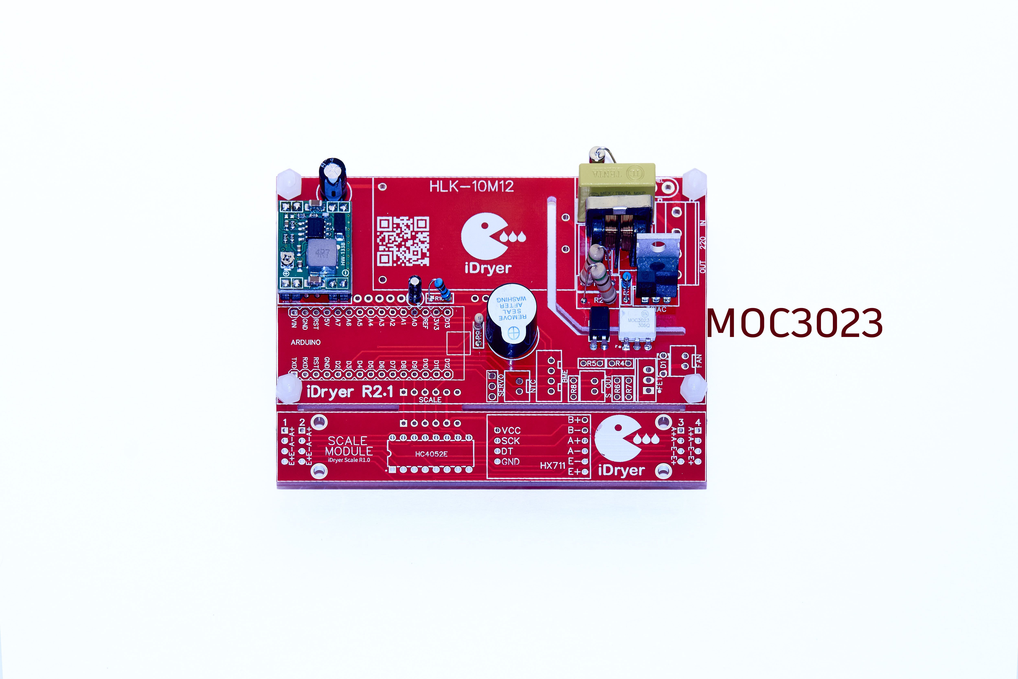
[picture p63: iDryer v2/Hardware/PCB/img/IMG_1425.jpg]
iDryer сборка контроллера сушилки филамента
    
  </div>
</div>

<div class="image-container">
  <div class="custom-image">
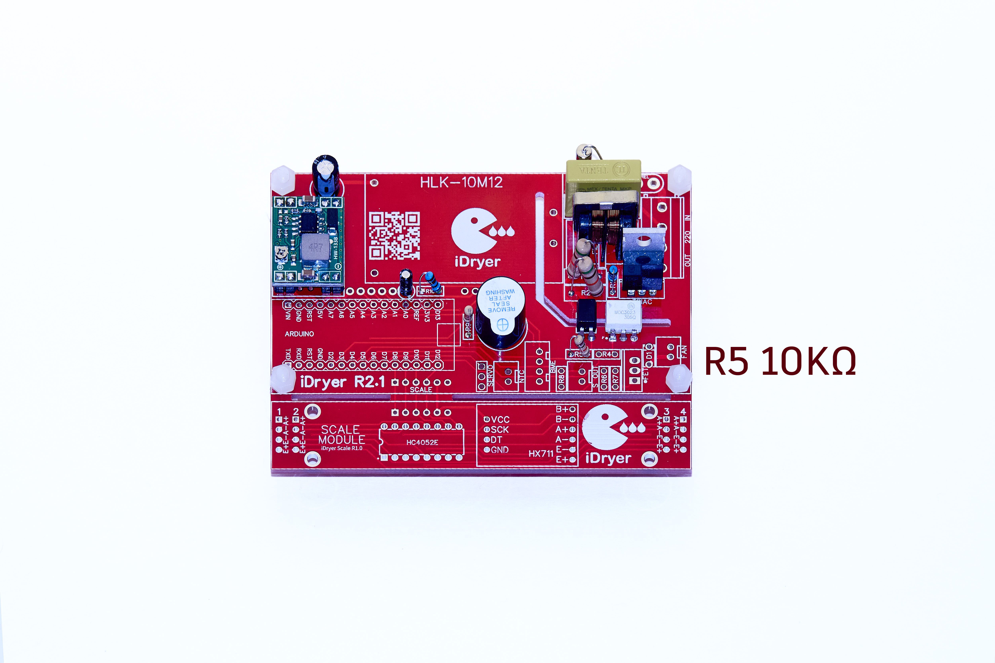
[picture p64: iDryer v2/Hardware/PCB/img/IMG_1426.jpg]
iDryer сборка контроллера сушилки филамента
    
  </div>
  <div class="custom-image">
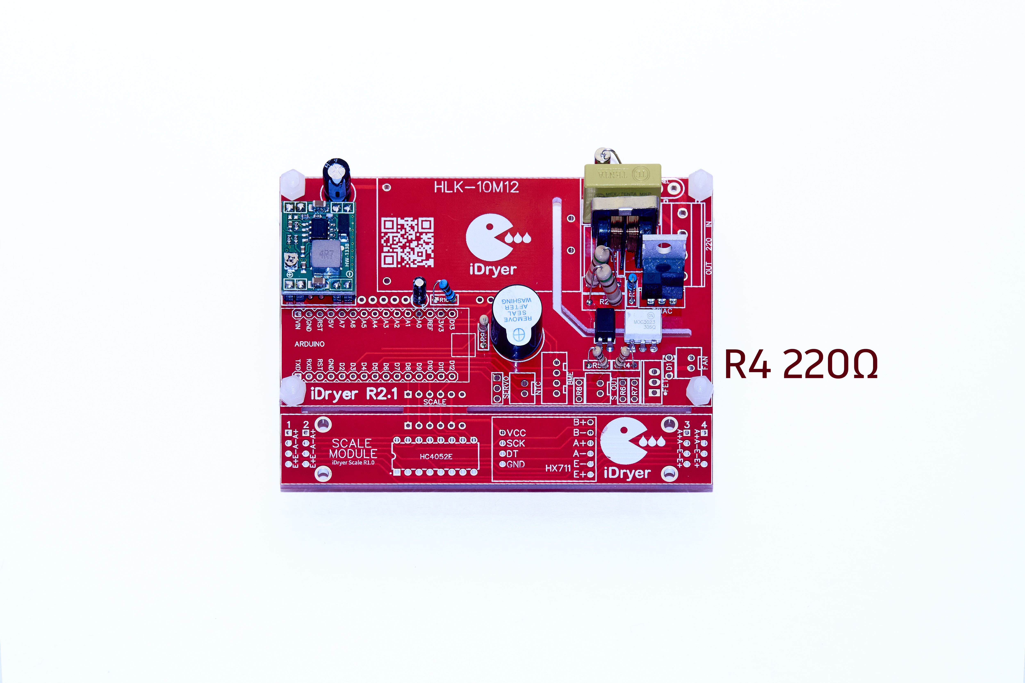
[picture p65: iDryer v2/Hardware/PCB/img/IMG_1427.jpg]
iDryer сборка контроллера сушилки филамента
    
  </div>
  <div class="custom-image">
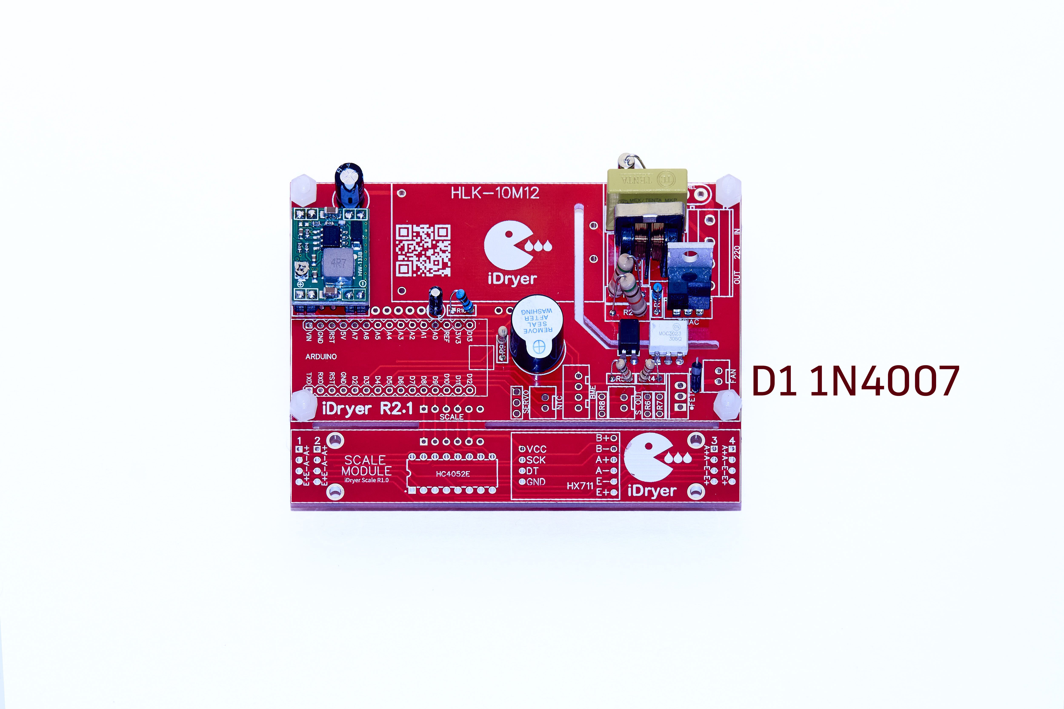
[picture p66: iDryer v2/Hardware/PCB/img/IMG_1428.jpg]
iDryer сборка контроллера сушилки филамента
    
  </div>
</div>

<div class="image-container">
  <div class="custom-image">
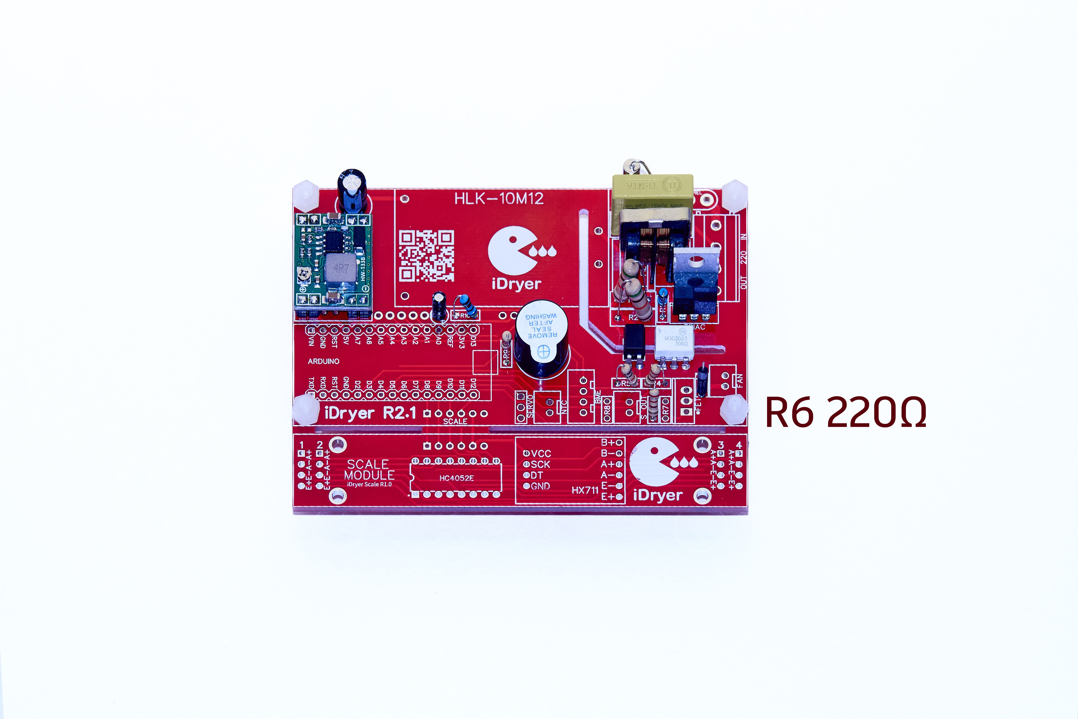
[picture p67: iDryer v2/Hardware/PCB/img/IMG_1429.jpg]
iDryer сборка контроллера сушилки филамента
    
  </div>
  <div class="custom-image">
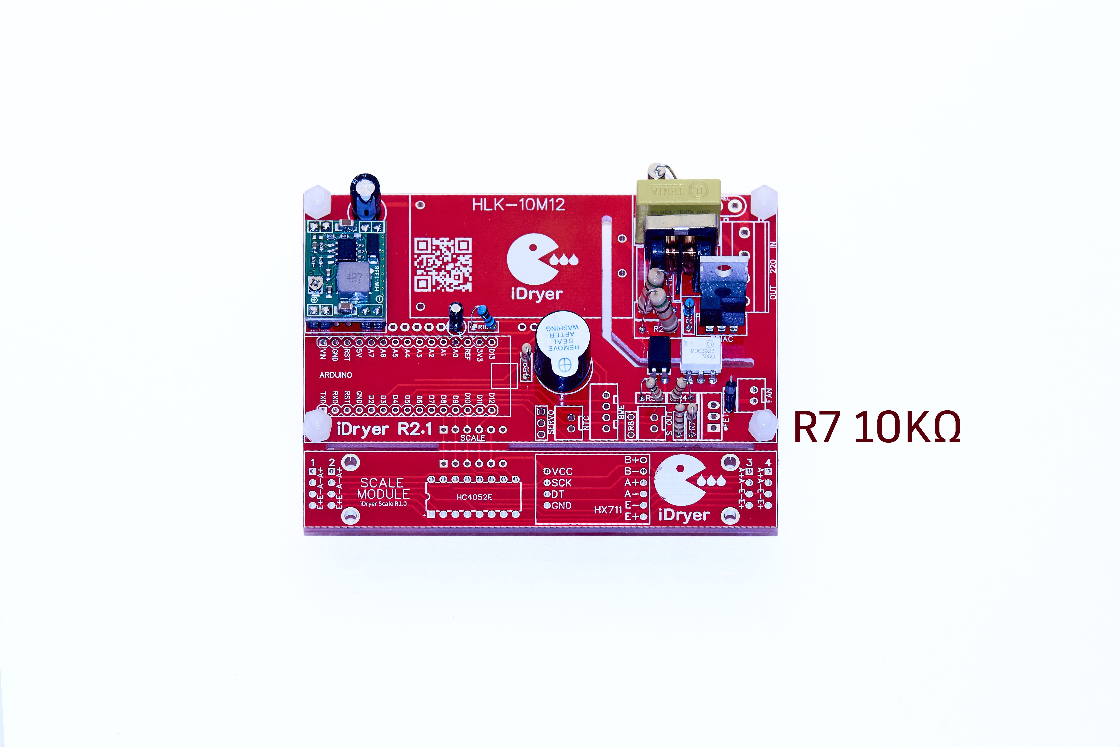
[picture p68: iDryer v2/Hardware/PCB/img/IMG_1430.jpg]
iDryer сборка контроллера сушилки филамента
    
  </div>
  <div class="custom-image">
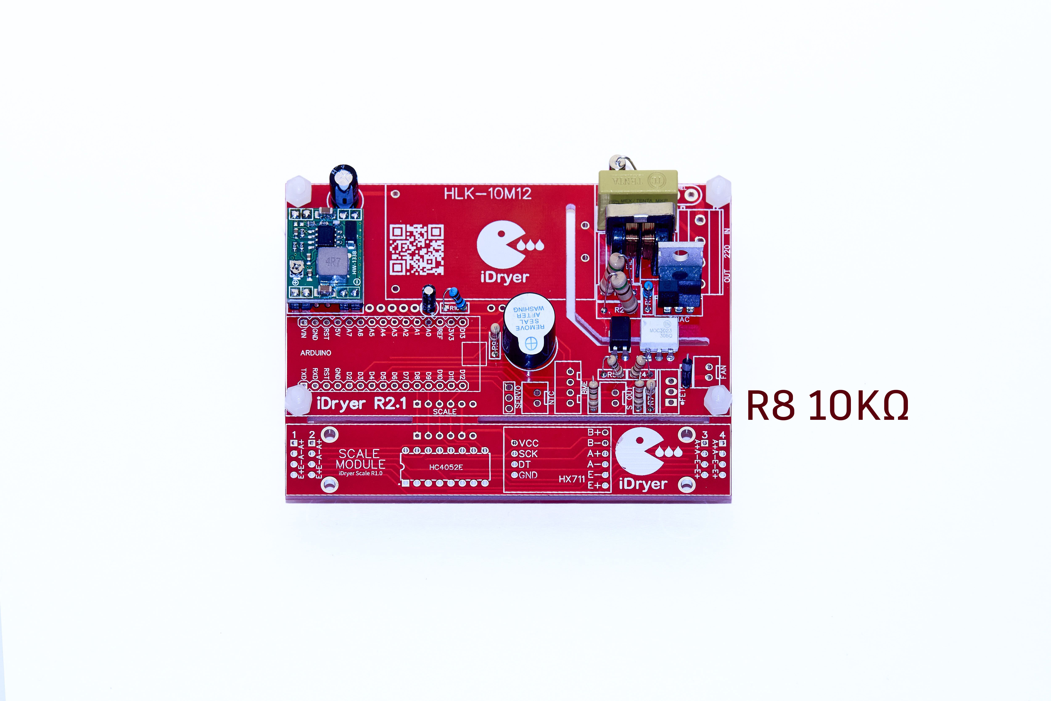
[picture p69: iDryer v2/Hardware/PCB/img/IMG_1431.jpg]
iDryer сборка контроллера сушилки филамента
    
  </div>
</div>

<div class="image-container">
  <div class="custom-image">
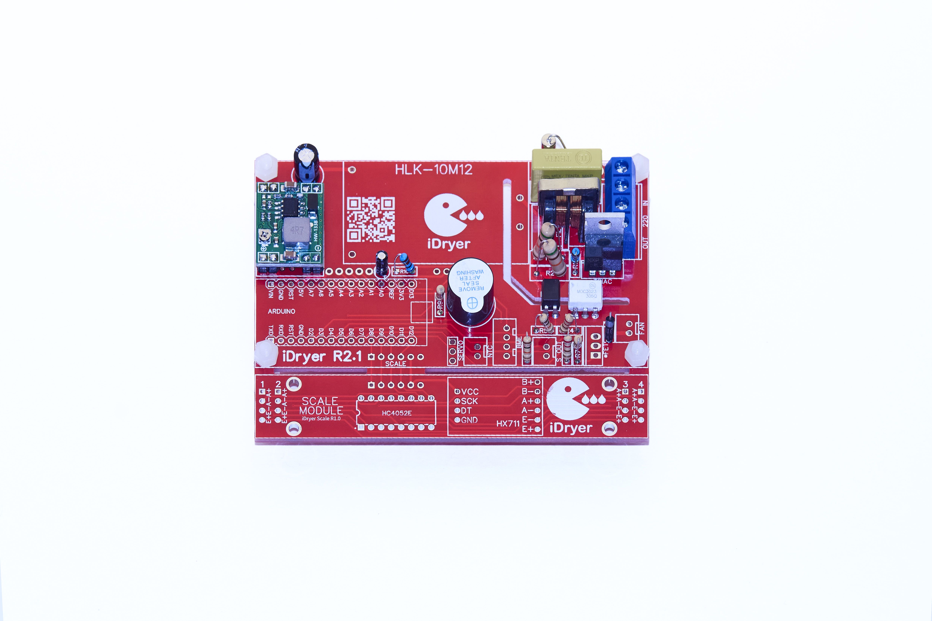
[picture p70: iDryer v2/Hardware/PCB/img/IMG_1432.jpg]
iDryer сборка контроллера сушилки филамента
    
  </div>
  <div class="custom-image">
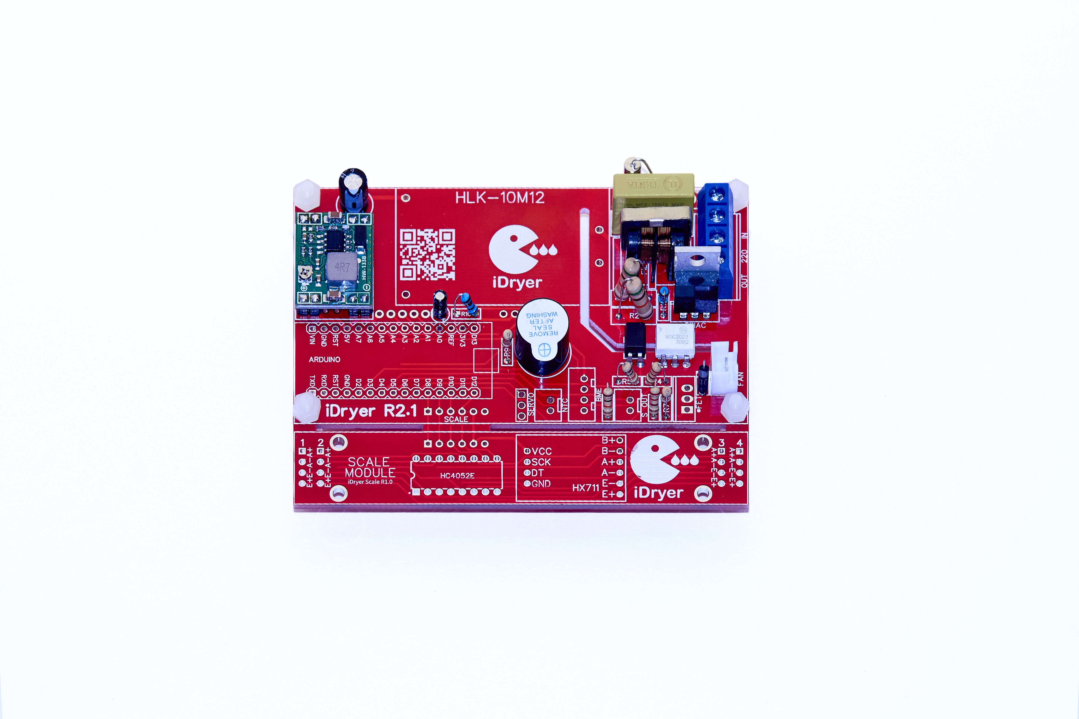
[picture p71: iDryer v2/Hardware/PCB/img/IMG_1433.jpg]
iDryer сборка контроллера сушилки филамента
    
  </div>
  <div class="custom-image">
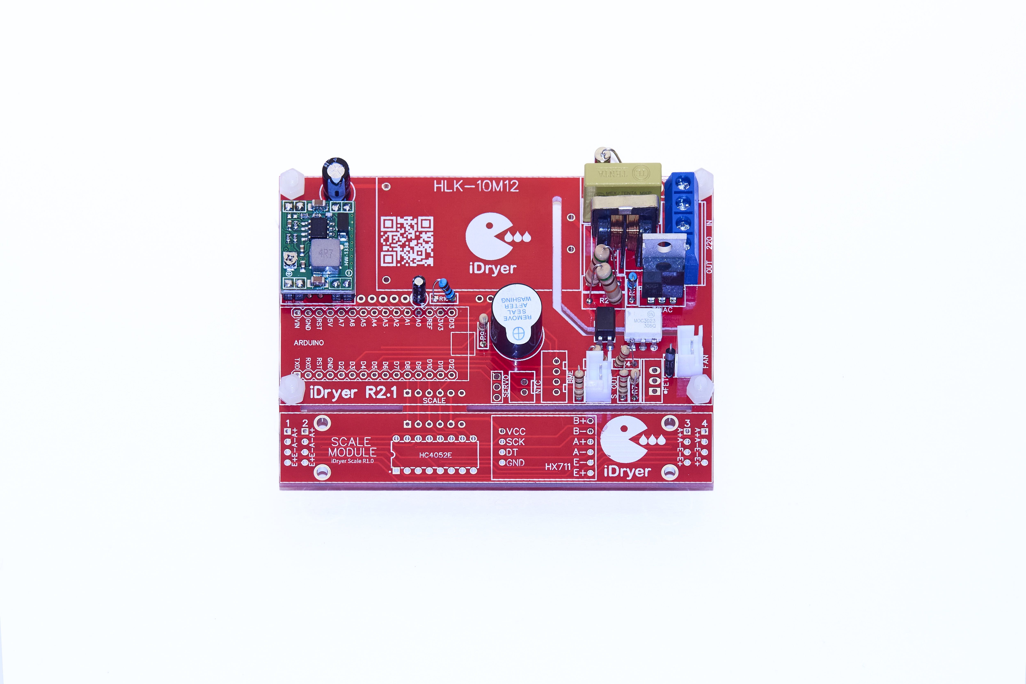
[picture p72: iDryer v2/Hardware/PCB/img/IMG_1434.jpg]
iDryer сборка контроллера сушилки филамента
    
  </div>
</div>

<div class="image-container">
  <div class="custom-image">
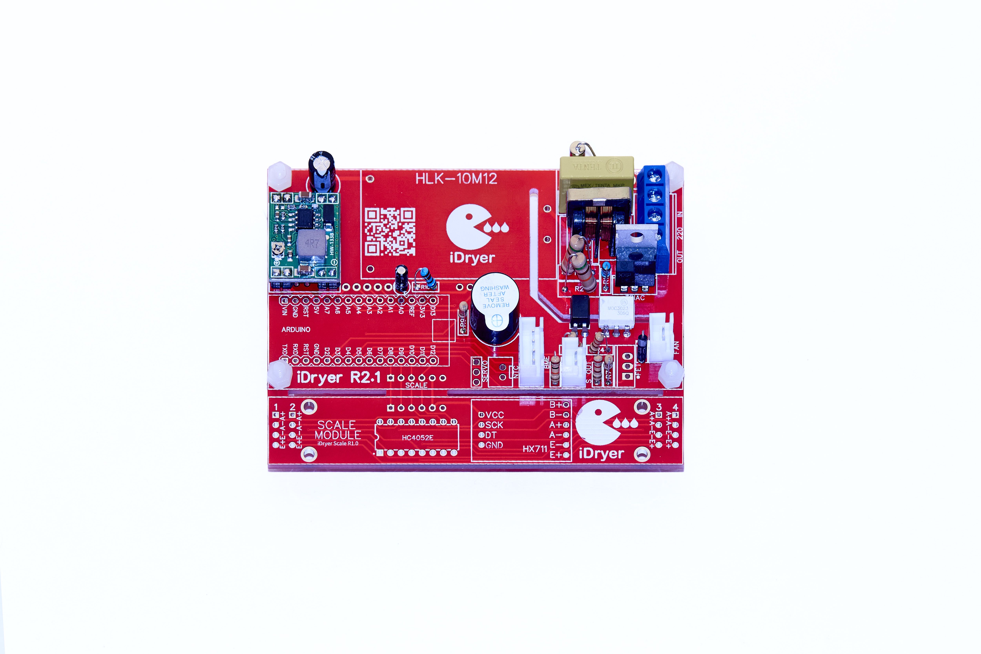
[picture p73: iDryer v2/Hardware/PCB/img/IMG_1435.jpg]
iDryer сборка контроллера сушилки филамента
    
  </div>
  <div class="custom-image">
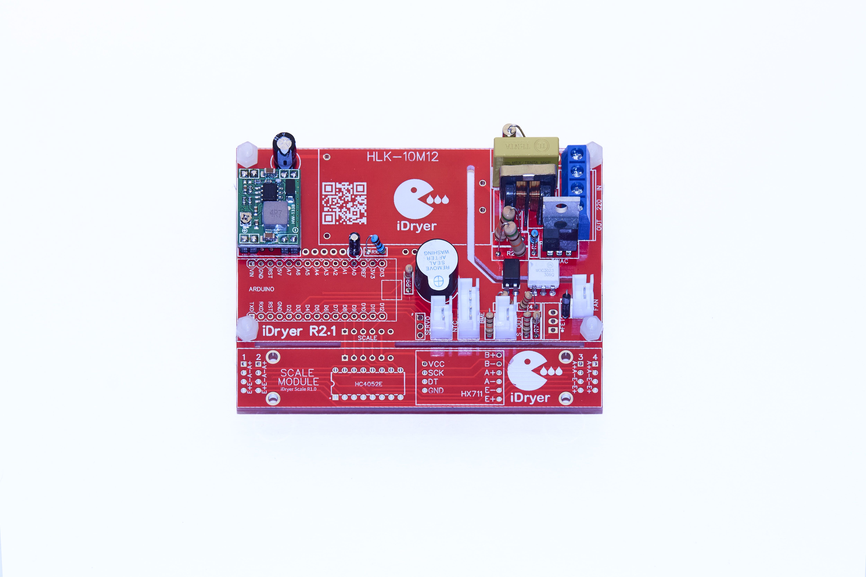
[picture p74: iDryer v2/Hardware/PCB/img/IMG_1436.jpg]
iDryer сборка контроллера сушилки филамента
    
  </div>
  <div class="custom-image">
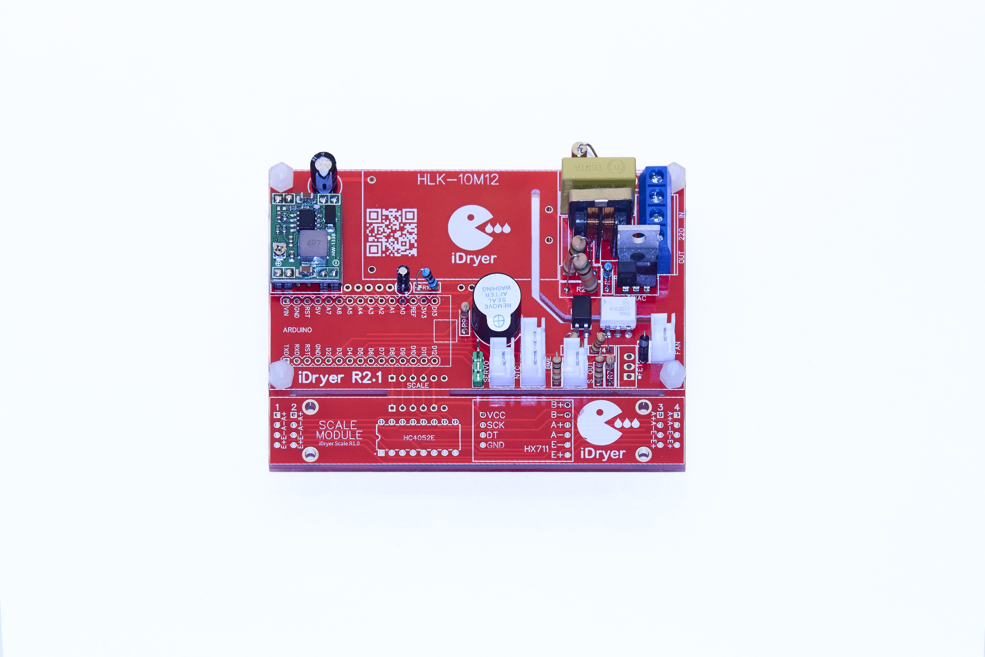
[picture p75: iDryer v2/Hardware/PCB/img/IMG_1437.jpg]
iDryer сборка контроллера сушилки филамента
    
  </div>
</div>

<div class="image-container">
  <div class="custom-image">
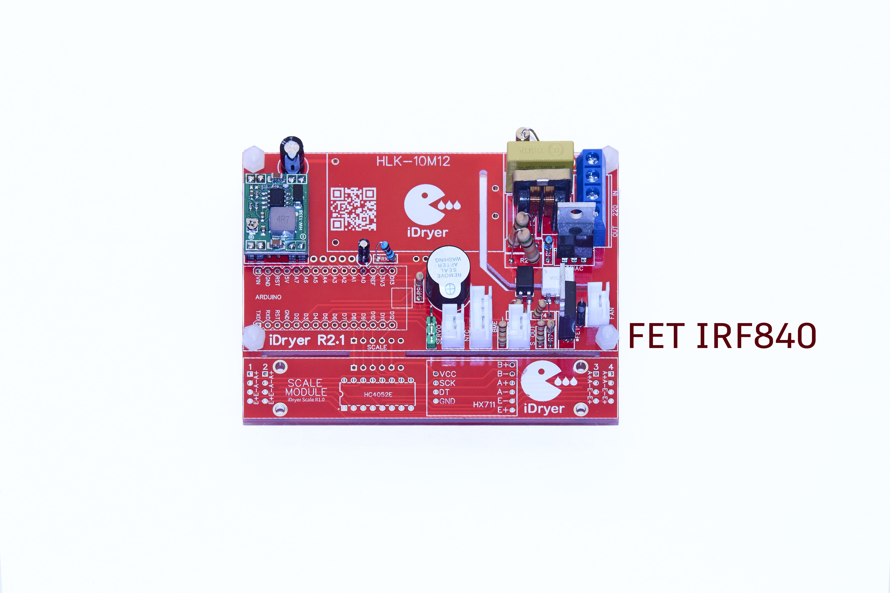
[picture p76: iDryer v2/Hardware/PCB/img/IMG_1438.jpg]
iDryer сборка контроллера сушилки филамента
    
  </div>
  <div class="custom-image">
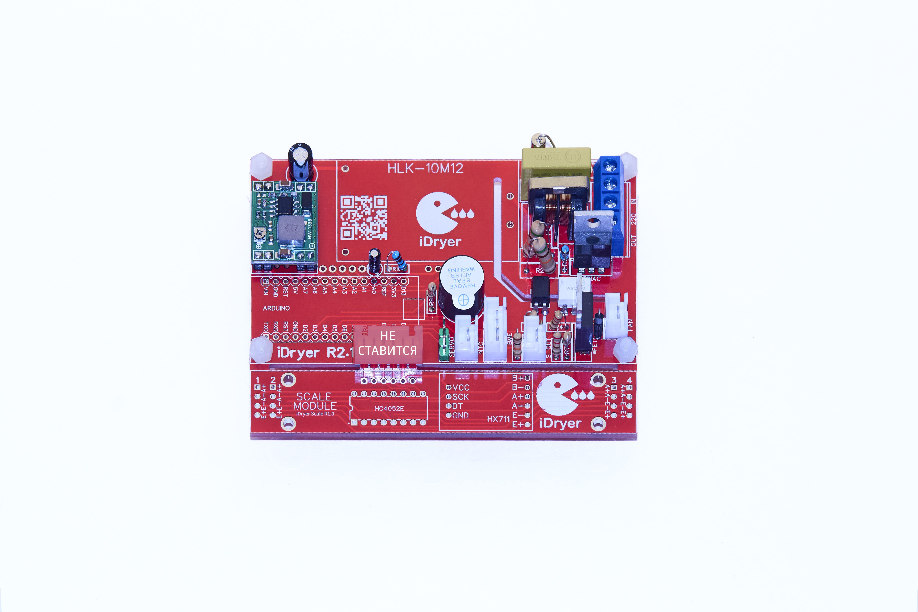
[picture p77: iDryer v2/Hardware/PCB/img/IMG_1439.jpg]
iDryer сборка контроллера сушилки филамента
    
  </div>
  <div class="custom-image">
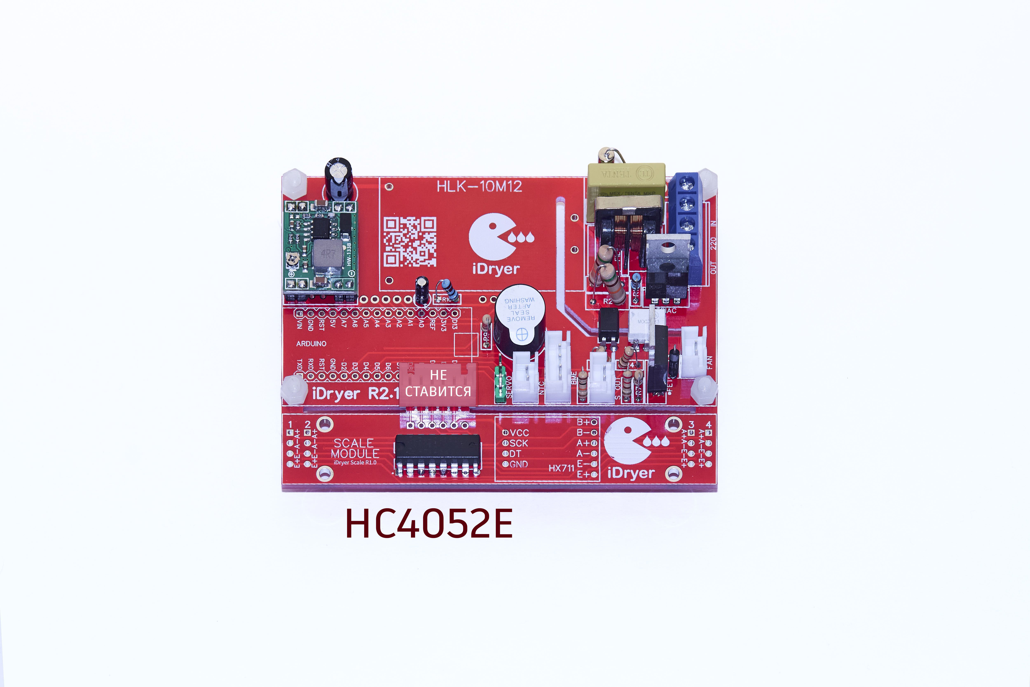
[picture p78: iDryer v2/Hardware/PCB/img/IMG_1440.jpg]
iDryer сборка контроллера сушилки филамента
    
  </div>
</div>

<div class="image-container">
  <div class="custom-image">
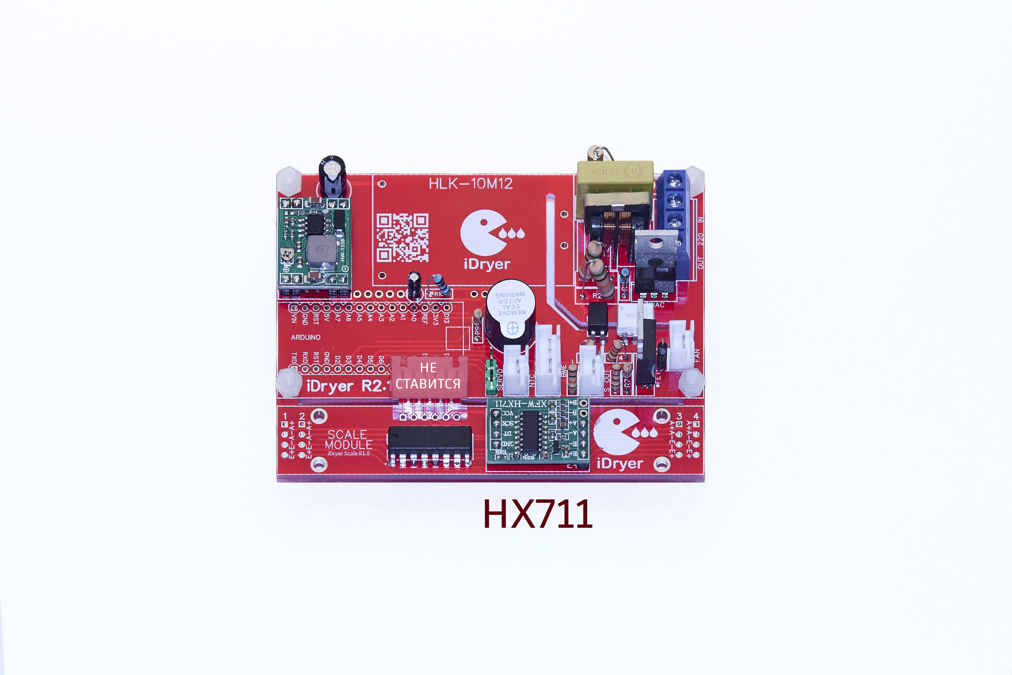
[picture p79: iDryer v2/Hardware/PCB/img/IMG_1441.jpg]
iDryer сборка контроллера сушилки филамента
    
  </div>
  <div class="custom-image">
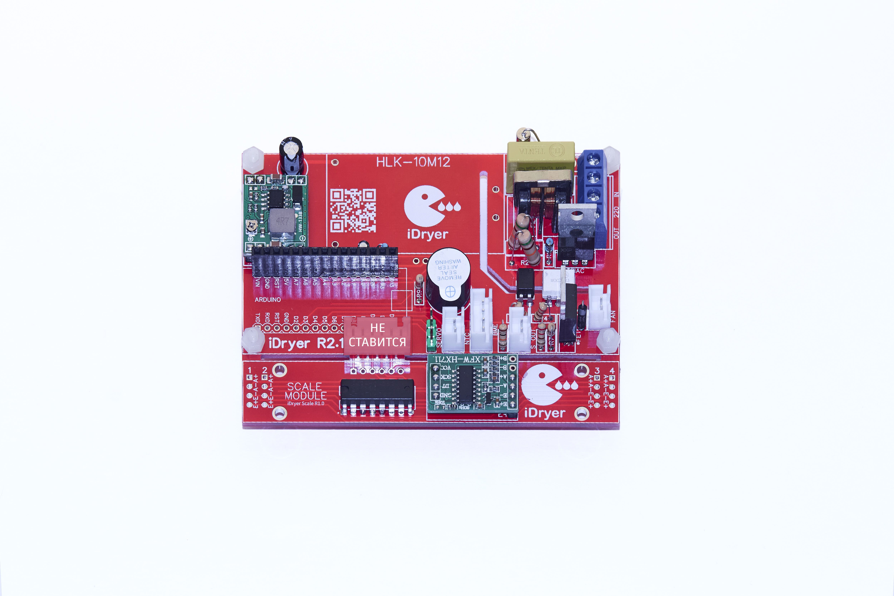
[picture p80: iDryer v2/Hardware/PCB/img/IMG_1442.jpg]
iDryer сборка контроллера сушилки филамента
    
  </div>
  <div class="custom-image">
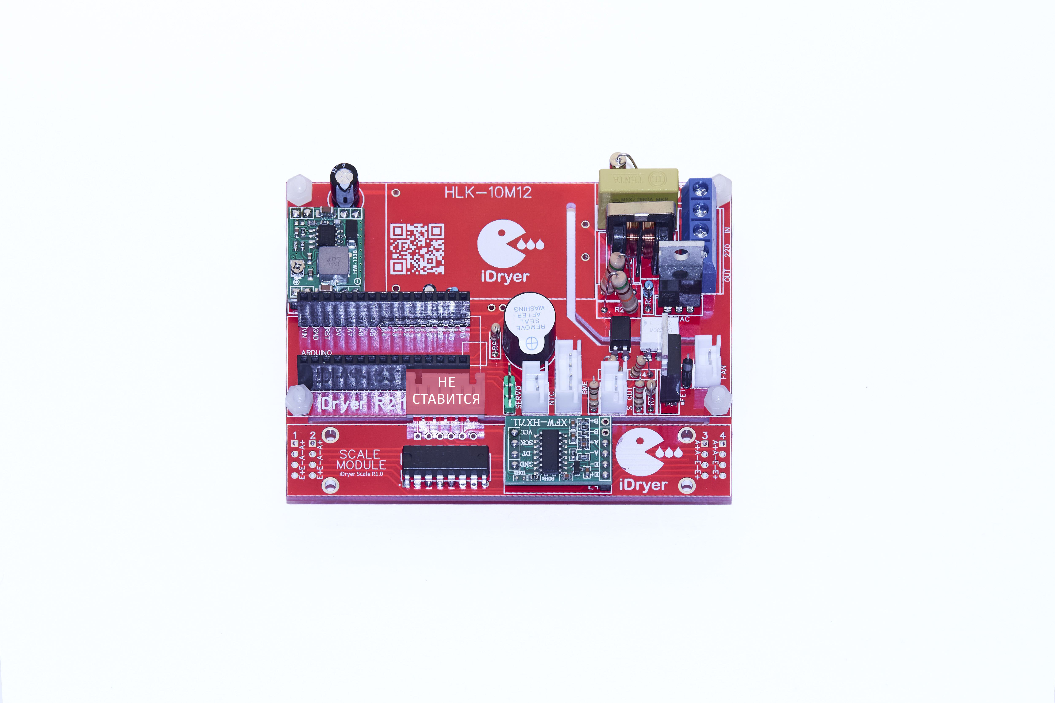
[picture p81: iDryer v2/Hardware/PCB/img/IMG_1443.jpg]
iDryer сборка контроллера сушилки филамента
    
  </div>
</div>

<div class="image-container">
  <div class="custom-image">
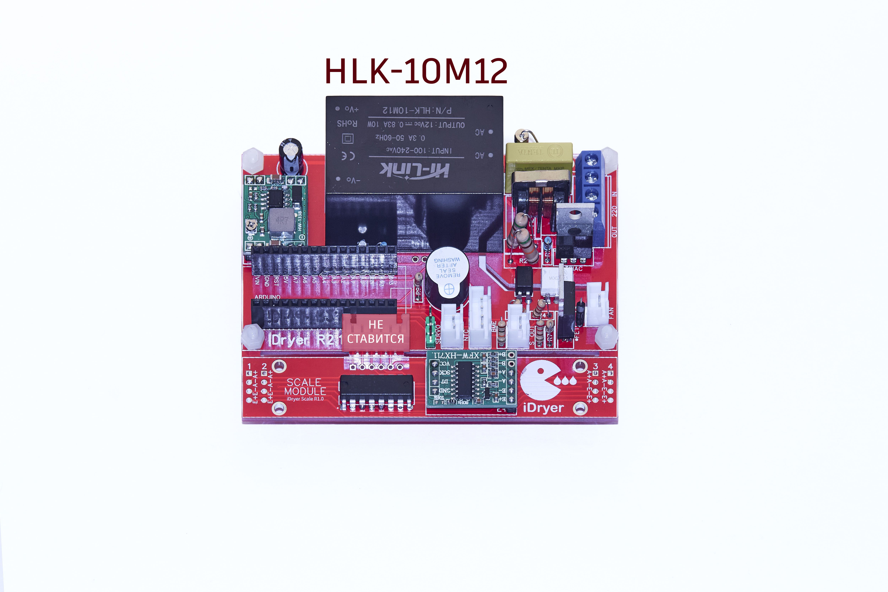
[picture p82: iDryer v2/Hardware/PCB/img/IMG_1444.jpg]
iDryer сборка контроллера сушилки филамента
    
  </div>
  <div class="custom-image">
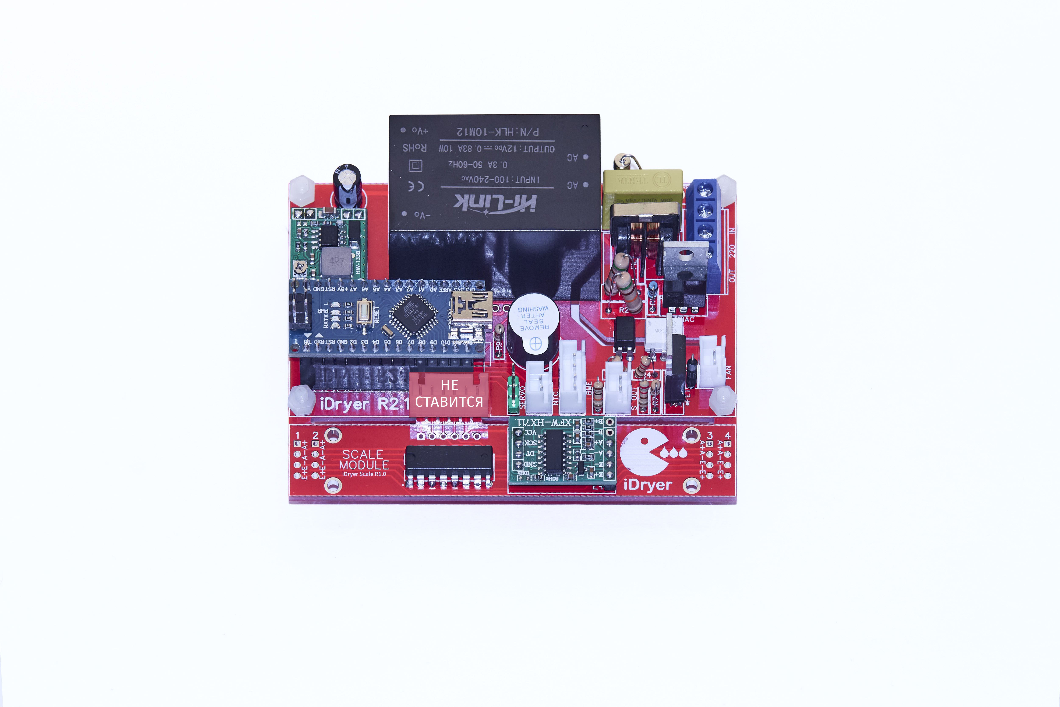
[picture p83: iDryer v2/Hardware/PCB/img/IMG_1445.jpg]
iDryer сборка контроллера сушилки филамента
    
  </div>
  <!-- <div class="custom-image">
    <img src="https://raw.githubusercontent.com/pavluchenkor/iDryerProject/main/iDryer%20v2/Hardware/PCB/img/IMG_1446.jpg" alt="iDryer сборка контроллера сушилки филамента">
  </div> -->
  <div class="custom-image">
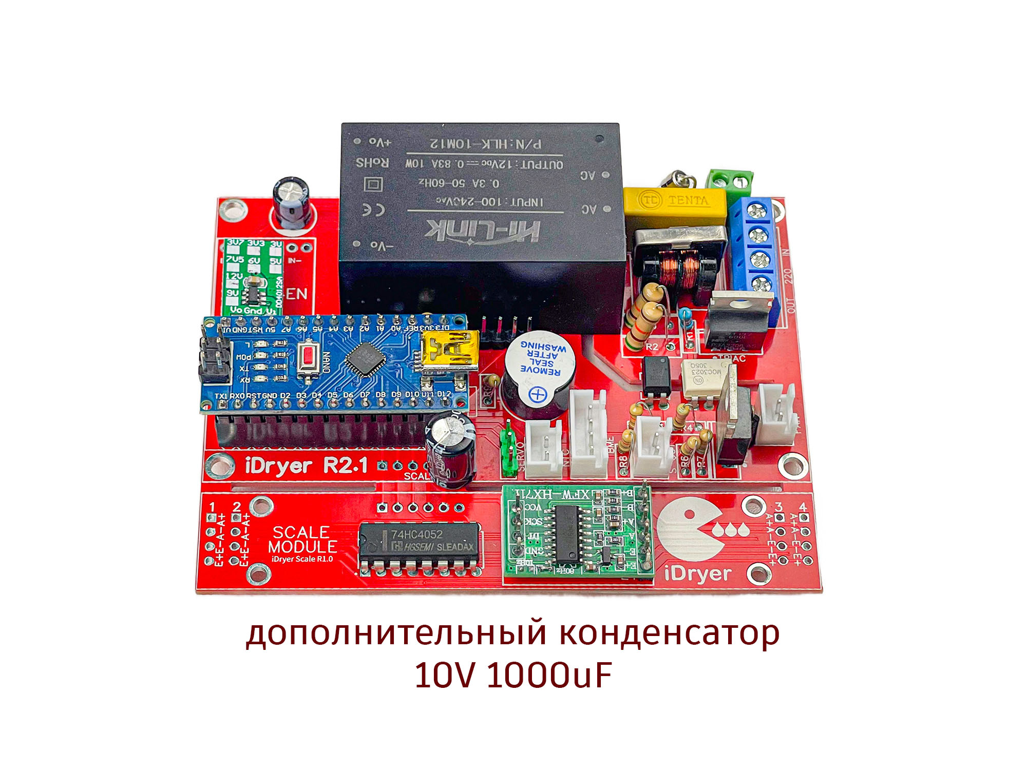
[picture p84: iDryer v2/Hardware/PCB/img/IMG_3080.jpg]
iDryer сборка контроллера сушилки филамента
    
  </div>
</div>

###Монтаж экрана и энкодера на плату

так нужно делать когда контроллер собирается в отдельном корпусе
<div class="image-container">
  <div class="custom-image">
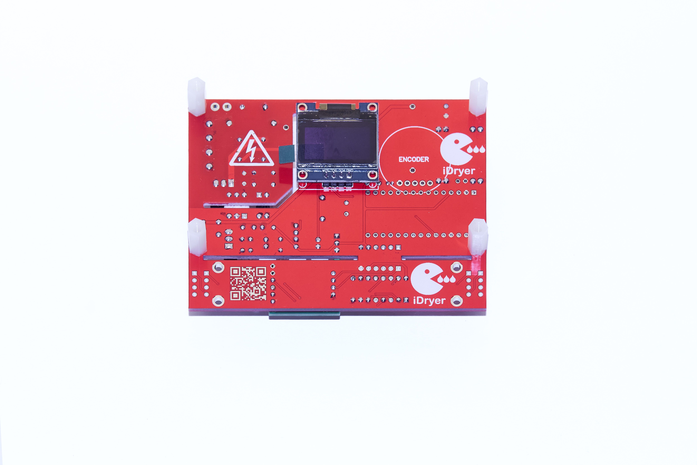
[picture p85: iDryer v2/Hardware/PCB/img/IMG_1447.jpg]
iDryer сборка контроллера сушилки филамента
    
  </div>
  <div class="custom-image">
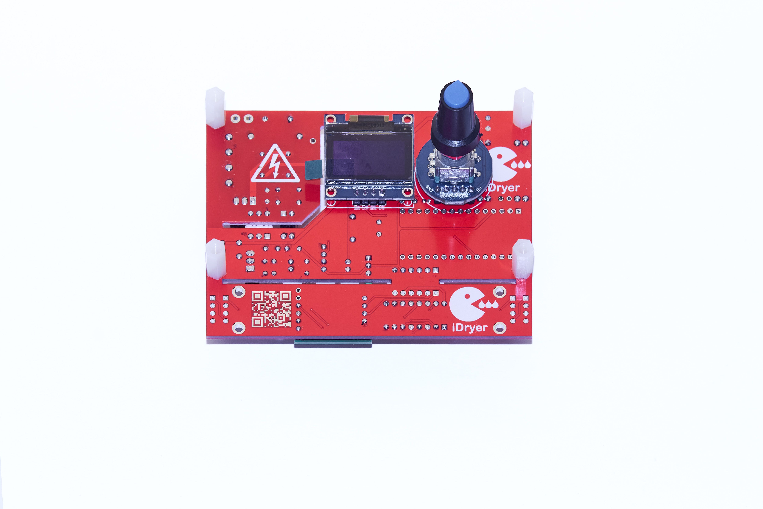
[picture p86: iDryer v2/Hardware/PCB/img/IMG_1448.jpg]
iDryer сборка контроллера сушилки филамента
    
  </div>
</div>

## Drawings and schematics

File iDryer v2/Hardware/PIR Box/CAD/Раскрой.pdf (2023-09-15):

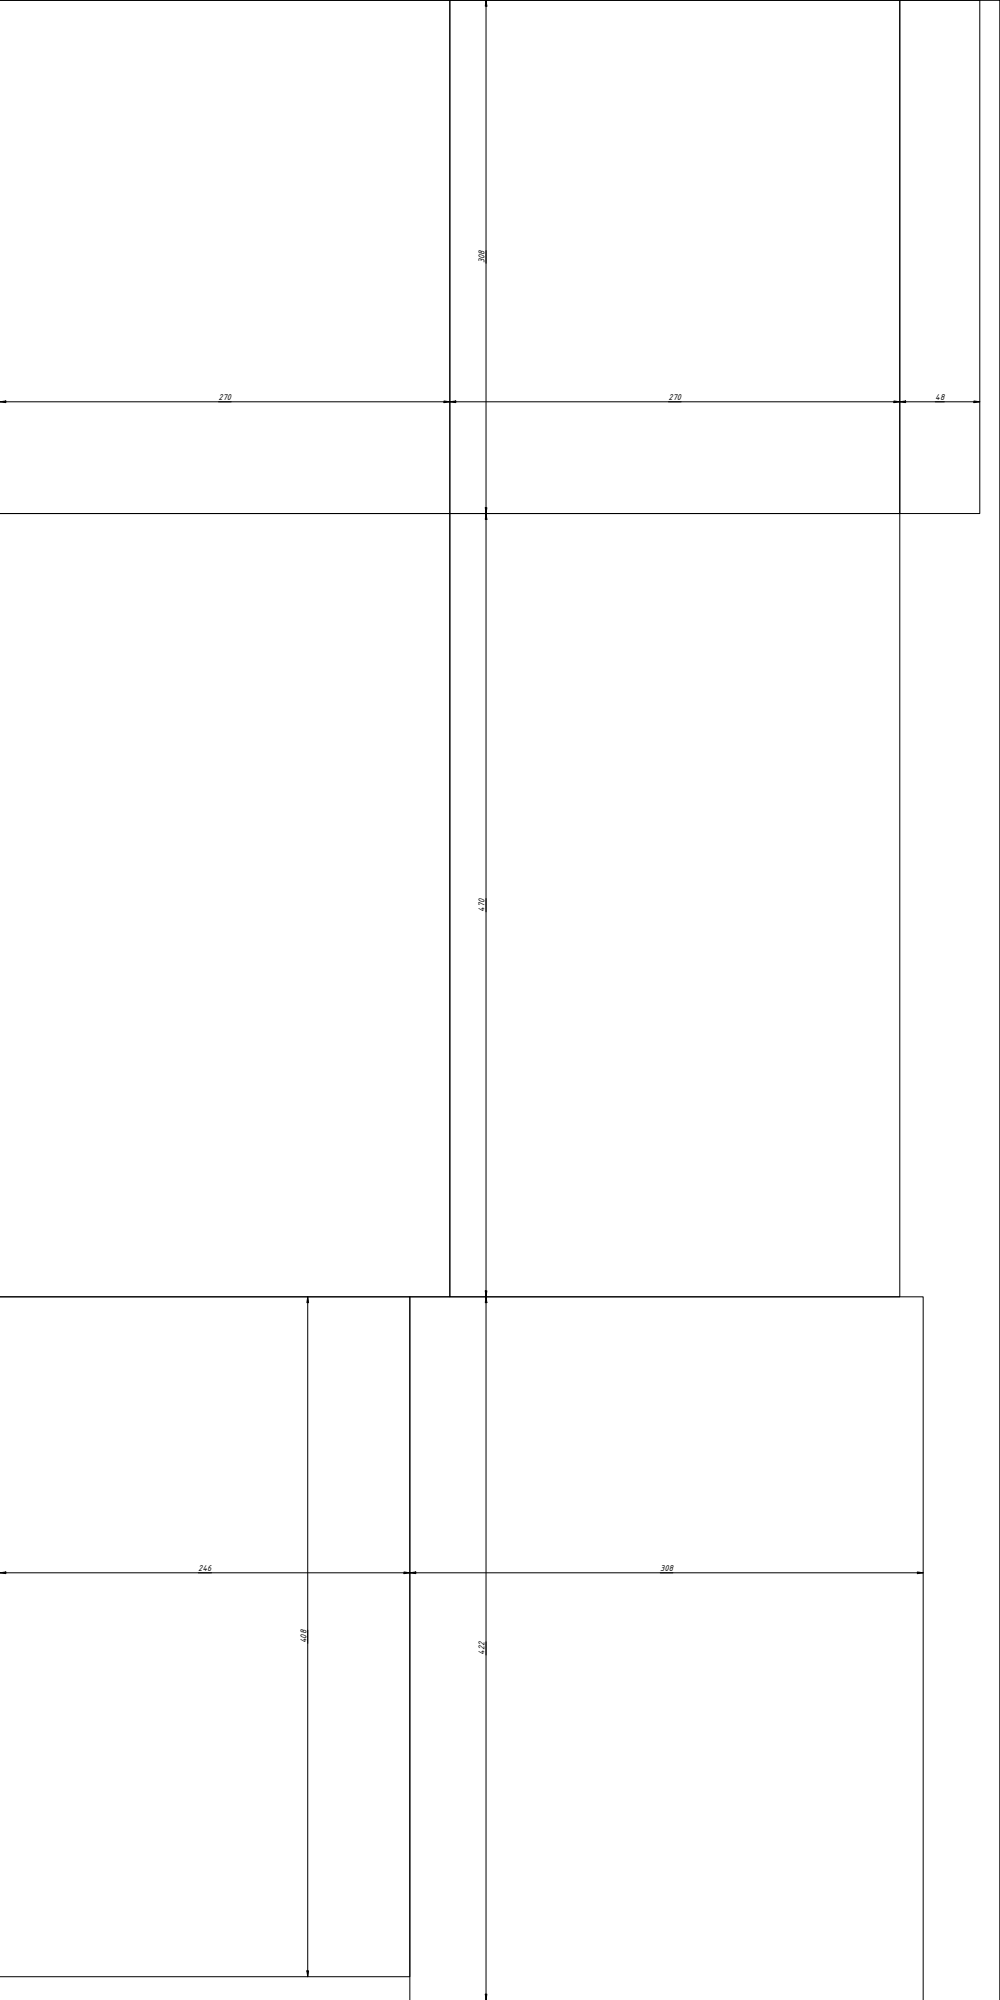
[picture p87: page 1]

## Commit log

2023-09-16 stl air damper add
    [air_damper_back.stl, air_damper_diffuser.stl, air_damper_flap.stl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]
2023-12-01 new Spool holder
    [Sasha.STEP]
2023-12-02 pir box assembly step add
    [PIR_box_assembly.stp]
2023-12-12 2.1 update
    [PIR_box_assembly.stp]
2023-12-16 2.1 pir add
    [PIR_box_assembly.stp]
2024-10-19 pinout img upd
    [PIR_box_assembly.stp]
2024-10-20 pcb manual upd
2024-10-22 3mf add
    [LogoPlate.3mf, iDryer_set1.3mf, iDryer_set2.3mf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]
2024-10-22 iDryer_set1.3mf upd
    [iDryer_set1.3mf]
2024-11-04 img add
    [панель_х2.3mf]
